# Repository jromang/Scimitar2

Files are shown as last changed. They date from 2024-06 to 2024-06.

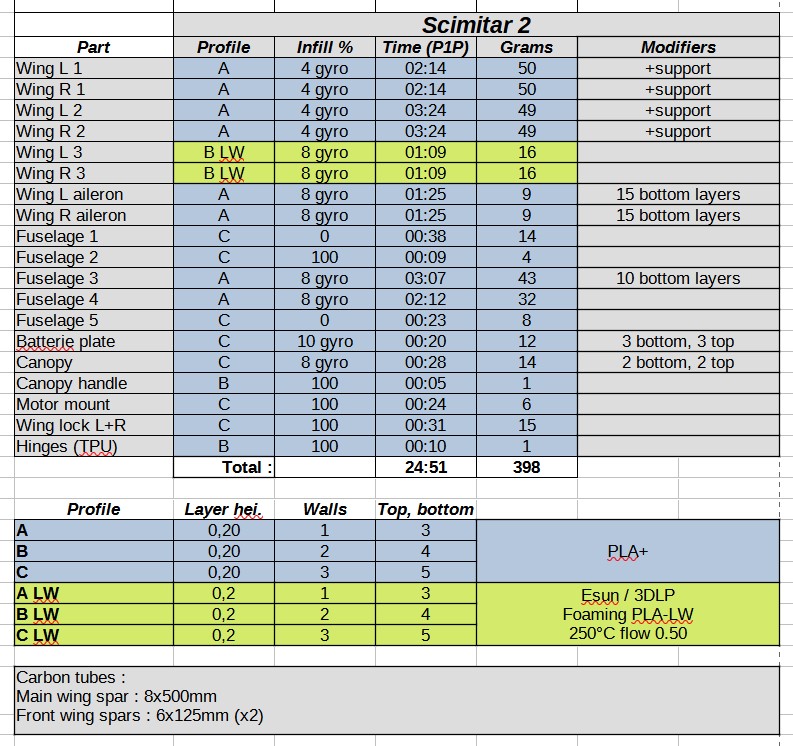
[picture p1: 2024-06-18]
Scimitar-parts.jpg

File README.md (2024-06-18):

# 3D printable wing by Olivier_C
[Original forum link](https://www.rcgroups.com/forums/showthread.php?4223695-Rifter-Sabre-Scimitar-mini-sized-FPV-cruisers)



End result is very slicer dependant.
Recommended material is PLA+ (Esun is great, but also Ender, Sunlu, Overture, etc), it also works with other materials and I try to anticipate for that as best as I can but the air gaps and dimensional constraints are made for PLA.

Bed size required : 200 x 200 x 220 high (mm)
(some models might need more)

First you'll have to create the 4 printing profiles, open your favorite 0.20mm-height profile that you know works fine on your printer :

- Set infill = 0%, walls = 1, top layers = 3, bottom layers = 3
- Save as profile A
- Set walls = 2, top layers = 4, bottom layers = 4
- Save as profile B
- Set walls = 3, top layers = 5, bottom layers = 5
- Save as profile C
- Re-open profile B, set infill = 100%
- Save as profile D

- Parts are in 3MF format, not centered on the printing plate, there's a folder in the package showing the correct orientation.
- By default printing with NO supports, NO infill (excepted the D profile, 100% infill). Then see the modifier column in the speadsheets.
- Wings on all the planes are perfectly symetrical left-right, so slice the left part, then use the mirror tool and slice again, there's no need to load the 3MF file for the other side.

It's important to print at the highest possible temperature to get a good fusion, as sample with Esun PLA+ I set 235°C

The files and models are free of charge, just if you can share photos and videos of your projects that'd be great 

Tracks really well, and can be printed very light with PLA-LW, is the simplest and the most modular, thus making it the obvious recommendation for a beginner.

# Assembling :

You will need :
- 6 or 8mm carbon tubes, exact lengths are listed in the spreadsheet for each plane
- Some M3 screws and nuts
- Few grams of TPU needed for the flexible ailerons hinges.
- Servo linkages are recommended with a ball joint, the rods are not always pulling perpendicular to the control surface.
- CA glue, with or without activator, works very well on PLA.
- Servo wells are made for Emax MD08/09 servos, standard micro size
- On all the flying wing types, ailerons needs a small amount of reflex up, 2mm at the trailing edge.

Wing span 80cm, length 41cm
Weight of the naked plane + 2 wing spars : 395gr
Weight of my plane with all FPV gear (FC, ESC, RX, 2 servos, antennas, HD camera +VTX), no battery : 540gr
AUW including 4S 1300mAh, 160gr battery : 700gr
Recommended motor : 2204-2206, 2306, F60
Recommended propeller : 6X4" to 6x5"
Battery : 4S, 150 to 230 grams.

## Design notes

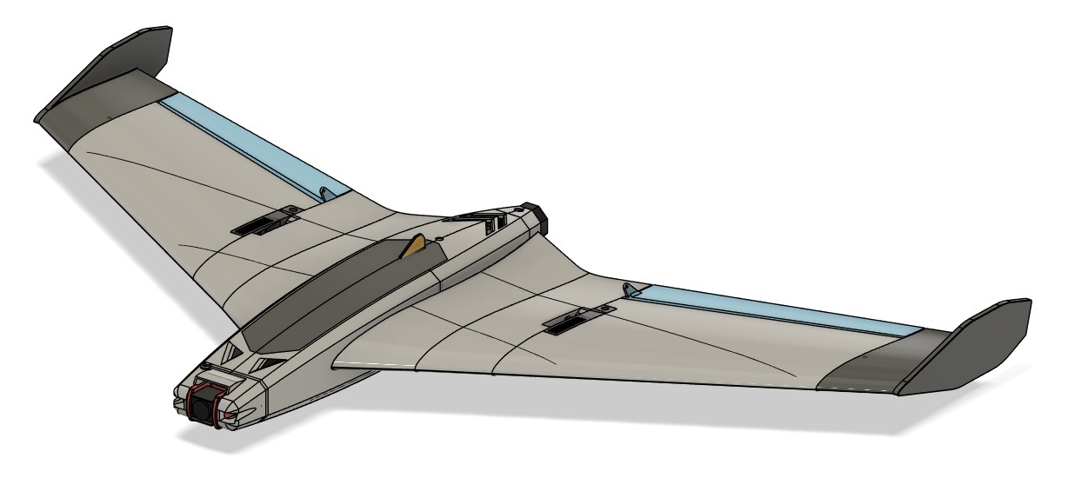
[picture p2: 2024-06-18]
Scimitar-front.jpg

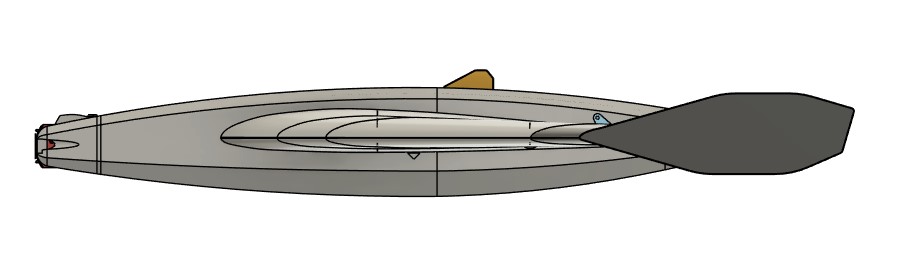
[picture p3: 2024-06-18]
Scimitar-side.jpg

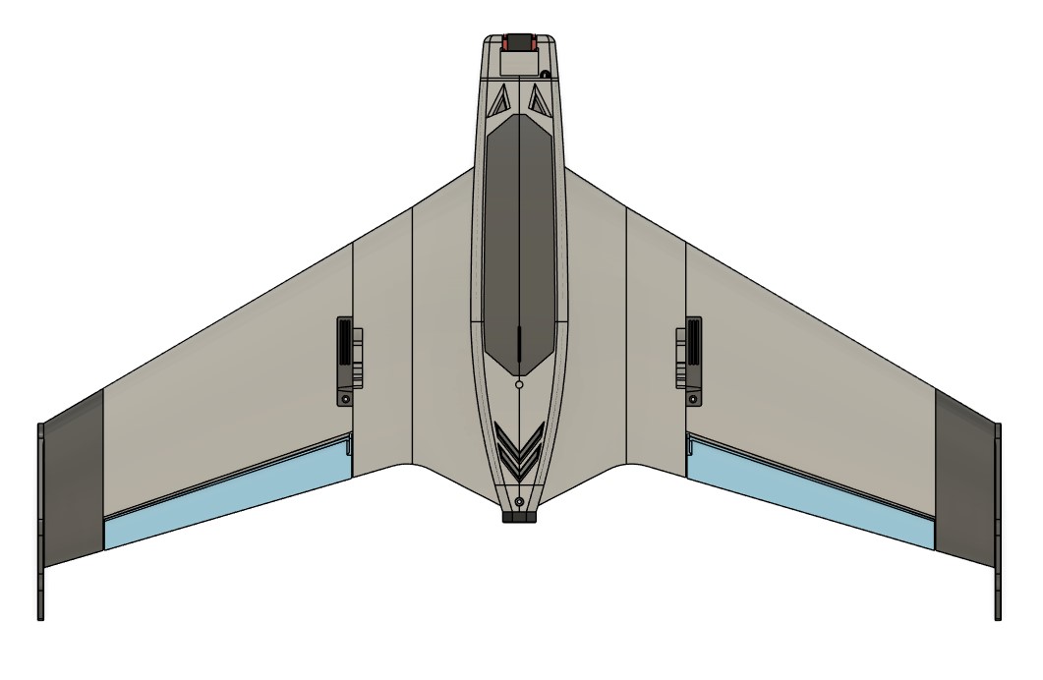
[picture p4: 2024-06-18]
Scimitar-top.jpg

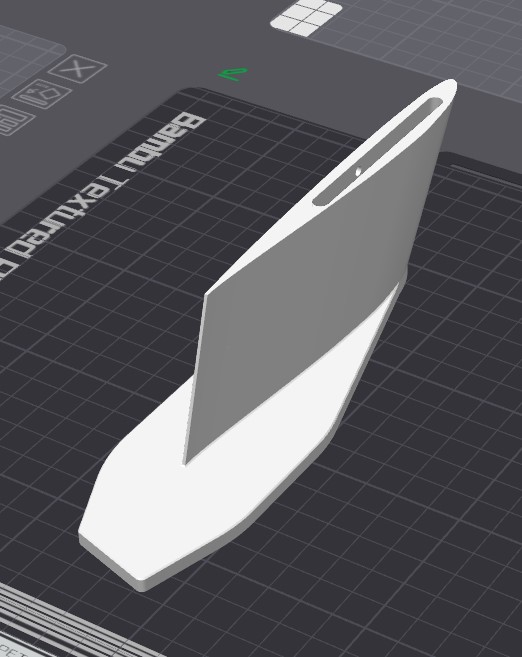
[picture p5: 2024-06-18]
Placement/Wing R 3.jpg

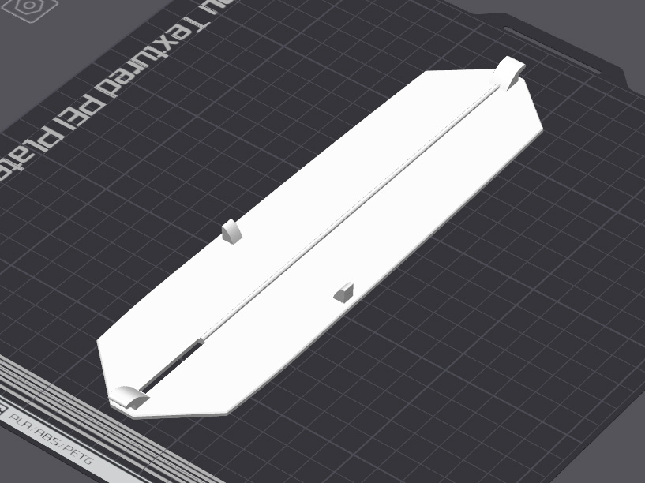
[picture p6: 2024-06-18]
Placement/Canopy.jpg

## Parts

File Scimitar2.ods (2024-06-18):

 | Scimitar 2
Part | Profile | Infill % | Time (P1P) | Grams | Modifiers
Wing L 1 | A | 4 gyro | 02:14 | 50 | +support
Wing R 1 | A | 4 gyro | 02:14 | 50 | +support
Wing L 2 | A | 4 gyro | 03:24 | 49 | +support
Wing R 2 | A | 4 gyro | 03:24 | 49 | +support
Wing L 3 | B LW | 8 gyro | 01:09 | 16
Wing R 3 | B LW | 8 gyro | 01:09 | 16
Wing L aileron | A | 8 gyro | 01:25 | 9 | 15 bottom layers
Wing R aileron | A | 8 gyro | 01:25 | 9 | 15 bottom layers
Fuselage 1 | C | 0 | 00:38 | 14
Fuselage 2 | C | 100 | 00:09 | 4
Fuselage 3 | A | 8 gyro | 03:07 | 43 | 10 bottom layers
Fuselage 4 | A | 8 gyro | 02:12 | 32
Fuselage 5 | C | 0 | 00:23 | 8
Batterie plate | C | 10 gyro | 00:20 | 12 | 3 bottom, 3 top
Canopy | C | 8 gyro | 00:28 | 14 | 2 bottom, 2 top
Canopy handle | B | 100 | 00:05 | 1
Motor mount | C | 100 | 00:24 | 6
Wing lock L+R | C | 100 | 00:31 | 15
Hinges (TPU) | B | 100 | 00:10 | 1
 | Total : |  | 24:51 | 398
Profile | Layer hei. | Walls | Top, bottom
A | 0,20 | 1 | 3 | PLA+
B | 0,20 | 2 | 4
C | 0,20 | 3 | 5
A LW | 0,2 | 1 | 3 | Esun / 3DLP Foaming PLA-LW 250°C flow 0.50
B LW | 0,2 | 2 | 4
C LW | 0,2 | 3 | 5
Carbon tubes : Main wing spar : 8x500mm Front wing spars : 6x125mm (x2)

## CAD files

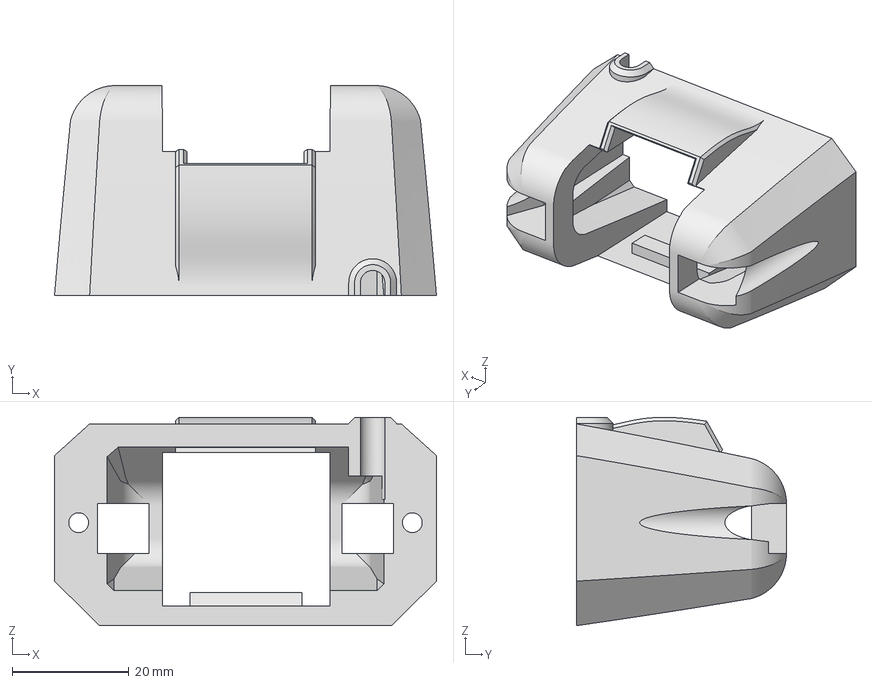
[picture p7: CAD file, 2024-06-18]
Extras/Fuselage 1 - SCM O3.3mf
65.5 x 36.0 x 35.7 mm

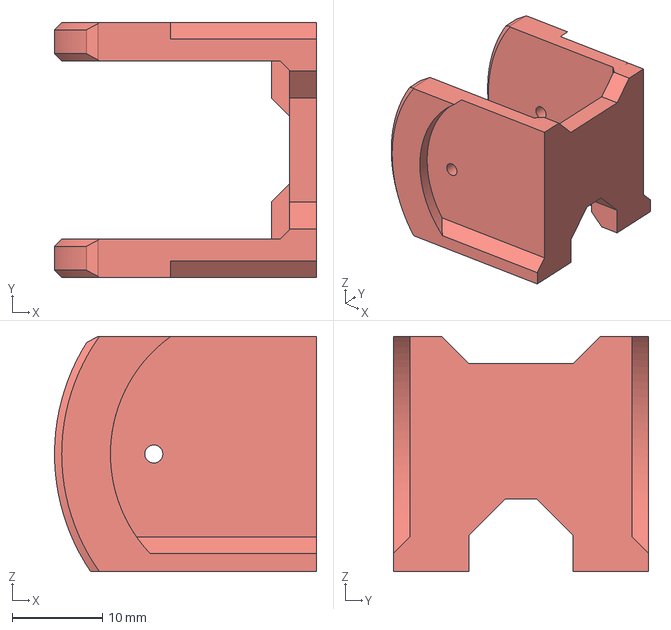
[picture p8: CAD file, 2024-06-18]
Extras/SCM - Standard camera mount/HDZero Micro Cam mount.3mf
29.0 x 28.2 x 26.0 mm

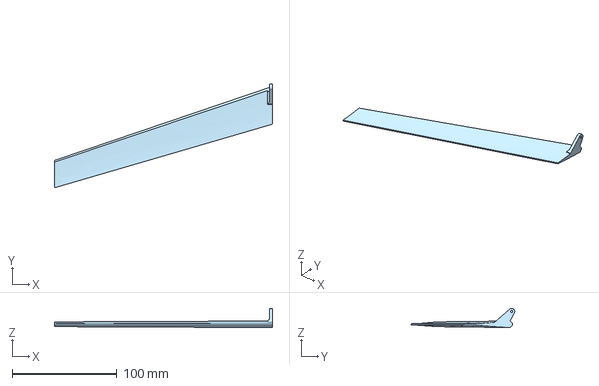
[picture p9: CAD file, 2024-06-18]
Extras/Step exports/Wing L Aileron.step
208.0 x 98.8 x 18.3 mm

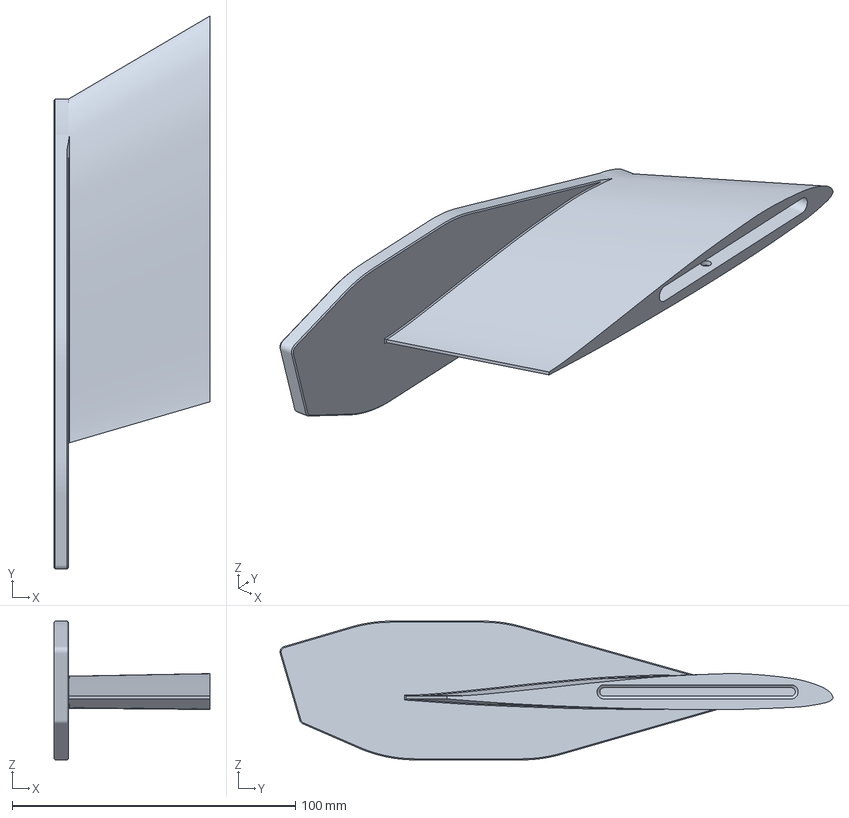
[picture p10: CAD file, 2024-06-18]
Parts/Wing L 3.3mf
55.0 x 195.2 x 49.0 mm

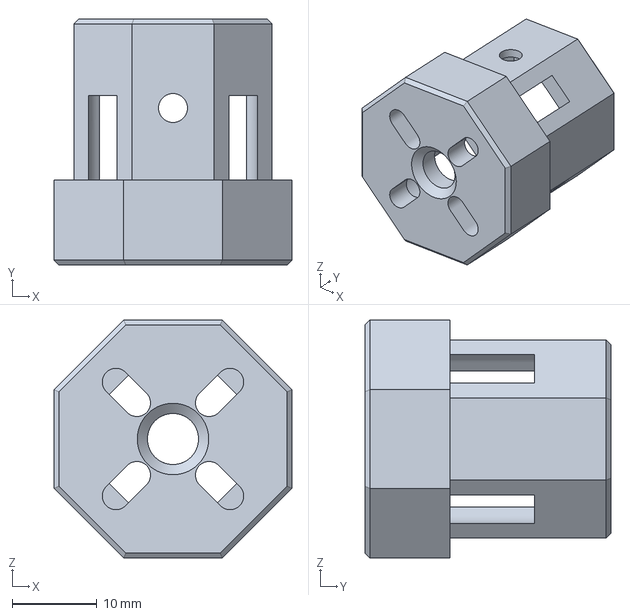
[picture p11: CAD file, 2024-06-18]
Extras/Motor mount 4mm.3mf
28.0 x 29.0 x 28.0 mm

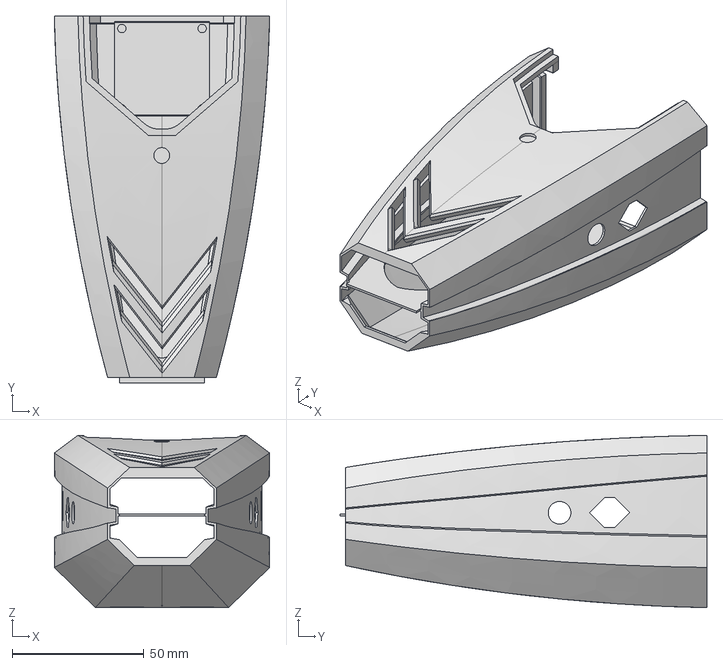
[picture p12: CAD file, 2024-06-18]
Extras/Step exports/Fuselage 4.step
81.8 x 139.4 x 65.5 mm

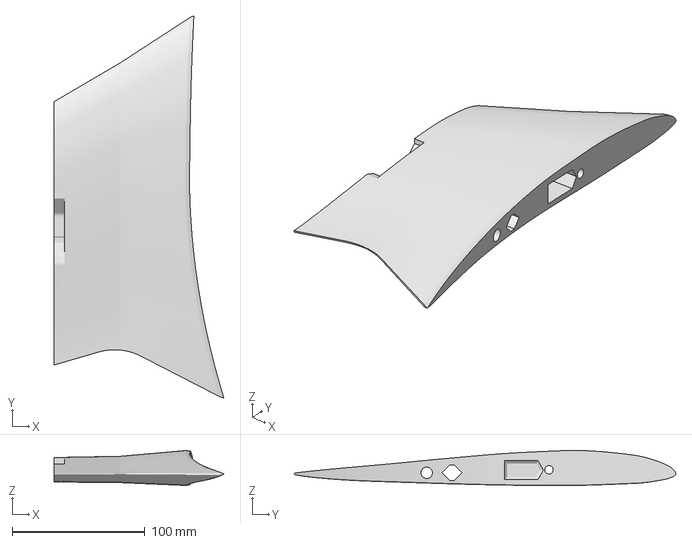
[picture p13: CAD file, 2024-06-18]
Parts/Wing L 1.3mf
127.9 x 287.6 x 26.4 mm

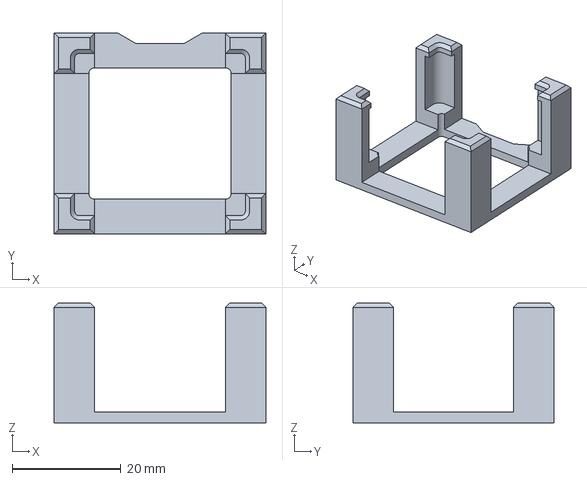
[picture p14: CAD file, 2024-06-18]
Extras/DJI O3 VTX mount.3mf
38.9 x 36.9 x 22.0 mm

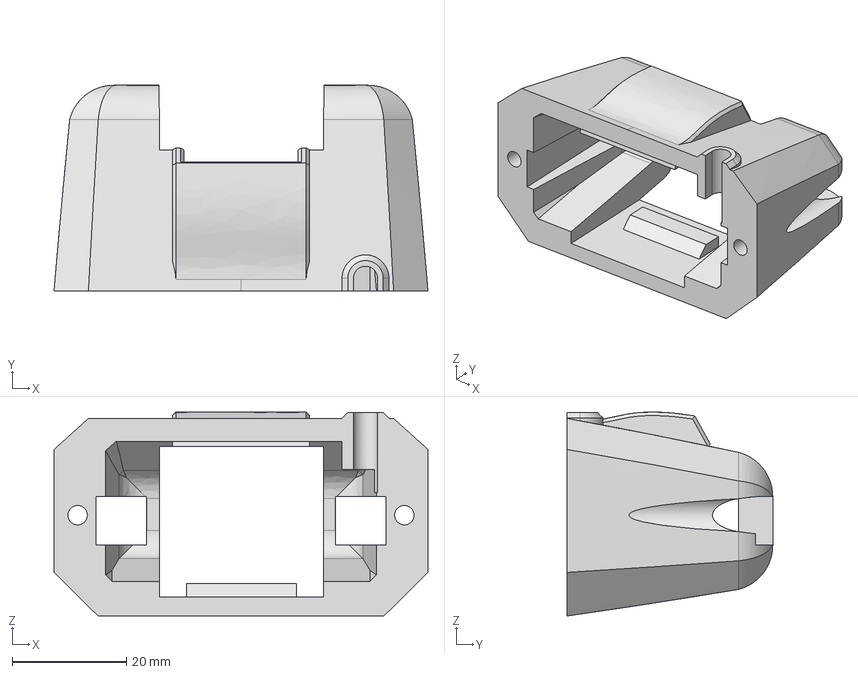
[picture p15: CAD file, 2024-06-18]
Extras/Step exports/Fuselage 1.step
65.5 x 36.0 x 35.7 mm

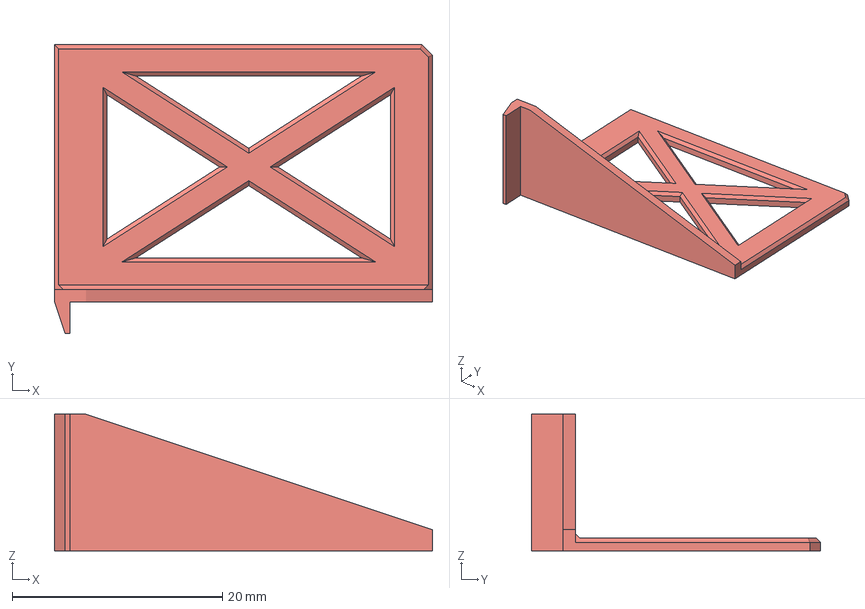
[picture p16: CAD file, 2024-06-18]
Extras/GPS mount R.3mf
36.0 x 27.5 x 13.0 mm

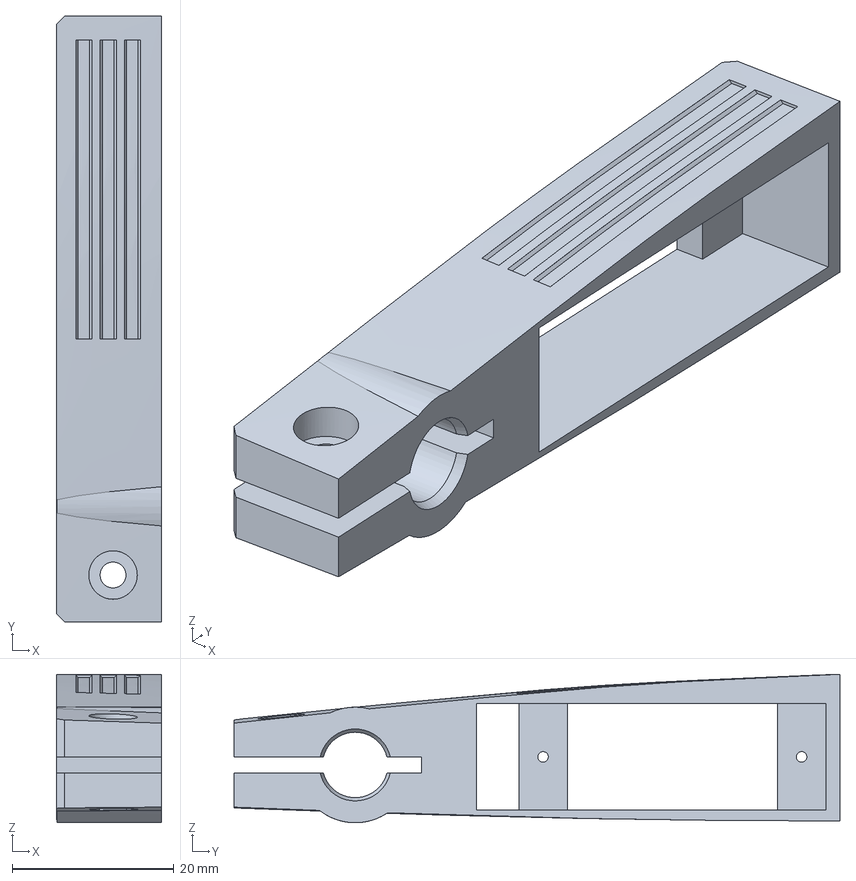
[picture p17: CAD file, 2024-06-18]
Extras/Step exports/Wing L Lock.step
13.0 x 75.0 x 18.4 mm

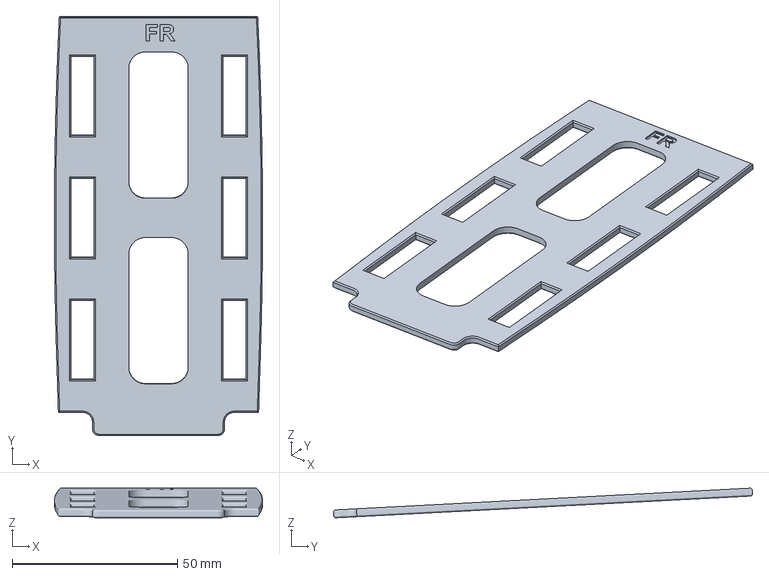
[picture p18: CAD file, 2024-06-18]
Parts/Battery plate.3mf
63.0 x 126.9 x 9.00 mm

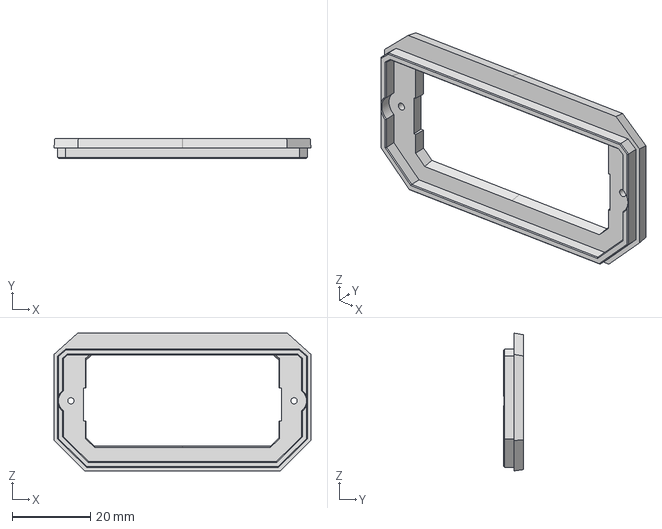
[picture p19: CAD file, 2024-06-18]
Extras/Step exports/Fuselage 2.step
65.9 x 5.00 x 35.4 mm

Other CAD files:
Extras/SCM - Standard camera mount/DJI O3 Cam mount.3mf
Extras/SCM - Standard camera mount/Walksnail Cam mount.3mf
Parts/Wing R Aileron.3mf
Extras/Step exports/Battery plate.step
Parts/Wing L Aileron.3mf
Extras/SCM - Standard camera mount/DJI O3 Camera.f3d
Extras/Step exports/Canopy.step
Extras/Step exports/Fuselage 3.step
Extras/Step exports/Fuselage 5.step
Extras/Step exports/Motor mount 3mm.step
Extras/Step exports/Wing L 1.step
Extras/Step exports/Wing L 2.step
Extras/Step exports/Wing L 3.step
Parts/Canopy handle.3mf
Parts/Canopy.3mf
Parts/Fuselage 1.3mf
Parts/Fuselage 2.3mf
Parts/Fuselage 3.3mf
Parts/Fuselage 4.3mf
Parts/Fuselage 5.3mf
Parts/Hinges TPU.3mf
Parts/Motor mount 3mm.3mf
Parts/Wing L 2.3mf
Parts/Wing L Lock.3mf
Parts/Wing R 1.3mf
Parts/Wing R 2.3mf
Parts/Wing R 3.3mf
Parts/Wing R Lock.3mf
